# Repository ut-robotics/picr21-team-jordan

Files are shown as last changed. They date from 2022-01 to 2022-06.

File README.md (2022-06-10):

## Project in competitive robotics 2021
</br>

**Credits:**</br>
Programming - **Leonid Tsigrinski**</br>
Mechanics - **Veronika Podliesnova** </br>
Electronics and firmware - **Valentin Resapow** </br>

<details><summary>Photos of Robot and PCB</summary>
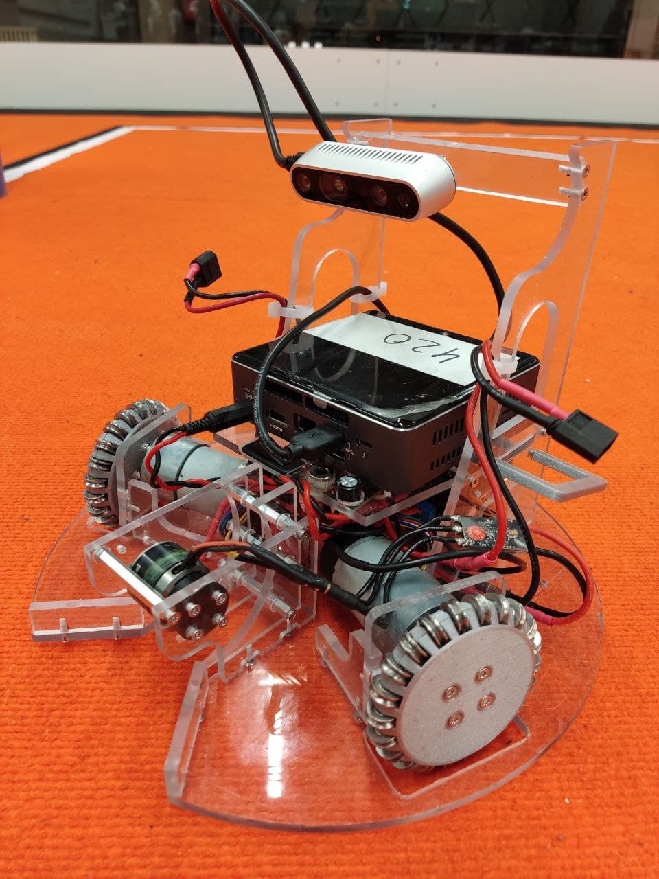
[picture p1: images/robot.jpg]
</br>
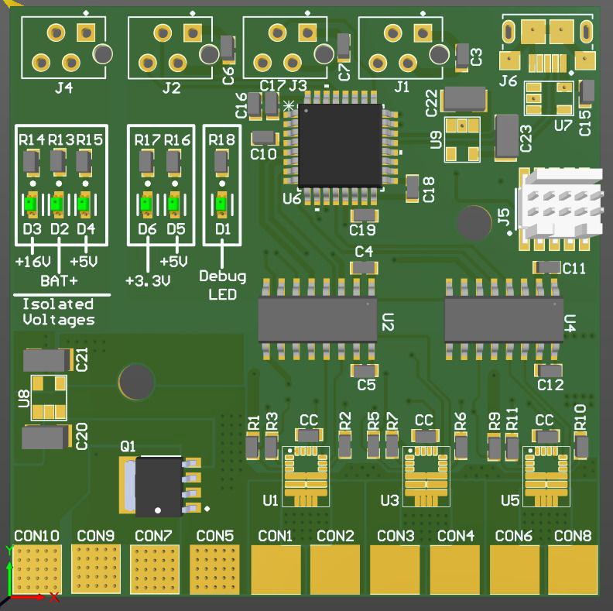
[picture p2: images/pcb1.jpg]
</br>
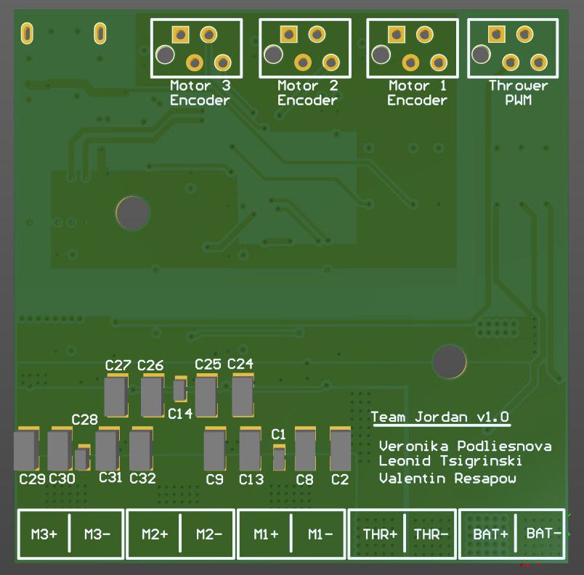
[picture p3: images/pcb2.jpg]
</br>
</details>

**Installation:**</br>
Move to project folder and run `python3.7 -m pip install -r requirements.txt`
Then go to the `.segment_module` folder and run `pip install .` 
Doesen't tested on other python version.</br>

**Used modules/libraries:**</br>
`Numpy` for image processing operations.</br>
`OpenCV` as optional GUI module.</br>
`Pyrealsense2` for realsense camera configuration and working with (especially getting depth).</br>
`Pyserial` for sending motor speed values (HW communication).</br>
`Websockets` for receiveng commands from referee. </br>
`Pynput` for robot manual control. </br>

**How to run the robot?:**</br>
Make sure, that you run first `image_calibration.py` file. Adjust all colors to be detected. Edit ip and port of the referee in `main.py` file, then run it. It you don't have any referees with their servers near by, run `_referee_server.py` . In server shell, you can send commands like "blue", "rose", and "stop", that will run the robot. In main shell, you can press the G to take manual control.

**Game logic:**  
Basically, there are two threads (asyncio coroutines), socket listener thread listens to to referee JSON data and fills global queue variable with it. Game Logic thread firstly checks if manual control enabled. Then checks if global queue variable were filled with commands. If it's a start command (with target basket), then the robot reads the camera image, gets the depth of the basked as well as coordinates of the basket and the balls. Then the robot selects the closest ball and moves to it, and for one iteration enables state machine algorithm. Every iteration state remains remembered. State machine by itself, it's just few steps:

-   find a ball (basically rotate)
-   get to a ball (calculate distance between ball x, y coords and the center coords. Distance is in linear dependency with axes speed)
-   find a basket (rotate around the ball until basket and the ball isn't centered)
-   throw (calculate throwing speed depends on the distance, linear dependency as well)

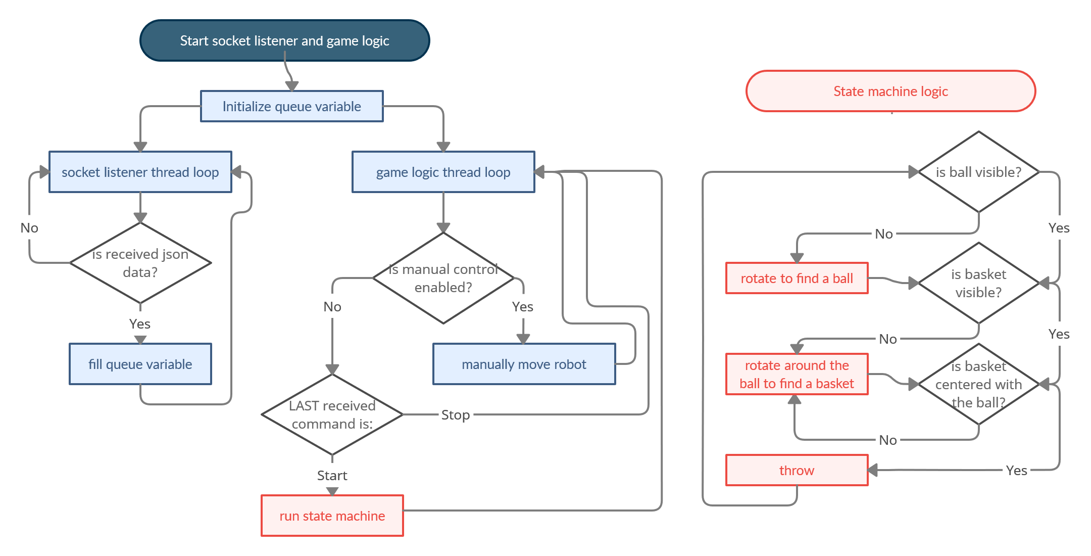
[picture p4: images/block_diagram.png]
</br>

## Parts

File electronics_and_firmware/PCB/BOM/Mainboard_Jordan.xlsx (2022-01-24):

Comment | Description | Designator | Footprint | LibRef | Quantity
Cap Semi | Capacitor (Semiconductor SIM Model) | C1, C3, C4, C5, C6, C7, C10, C11, C12, C14, C15, C16, C17, C18, C19, C28 | 1608[0603] | Cap Semi | 16
Cap Semi | Capacitor (Semiconductor SIM Model) | C2, C8, C9, C13, C20, C21, C22, C23, C24, C25, C26, C27, C29, C30, C31, C32 | C1206 | Cap Semi | 16
Res3 | Resistor | CC, R1, R2, R3, R5, R6, R7, R9, R10, R11, R13, R14, R15, R16, R17, R18 | J1-0603 | Res3 | 18
Moter1 + |  | CON1 | con_soldering | Con_soldering | 1
Motor1 - |  | CON2 | con_soldering | Con_soldering | 1
Motor2 + |  | CON3 | con_soldering | Con_soldering | 1
Motor2 - |  | CON4 | con_soldering | Con_soldering | 1
Thrower + |  | CON5 | con_soldering | Con_soldering | 1
Motor3 + |  | CON6 | con_soldering | Con_soldering | 1
Thrower - |  | CON7 | con_soldering | Con_soldering | 1
Motor3 - |  | CON8 | con_soldering | Con_soldering | 1
BAT+ |  | CON9 | con_soldering | Con_soldering | 1
BAT- |  | CON10 | con_soldering | Con_soldering | 1
LTST-C190GKT | LED GREEN CLEAR CHIP SMD | D1, D2, D3, D4, D5, D6 | FP-LTST-C190GKT-MFG | CMP-22017-000005-2 | 6
Encoder_1 | Micro-MaTch 4 Position 1.27 mm Pitch Vertical Female-on-Board Connector | J1 | TE_7-215079-4 | Con_4_encoder | 1
Encoder_2 | Micro-MaTch 4 Position 1.27 mm Pitch Vertical Female-on-Board Connector | J2 | TE_7-215079-4 | Con_4_encoder | 1
Encoder_3 | Micro-MaTch 4 Position 1.27 mm Pitch Vertical Female-on-Board Connector | J3 | TE_7-215079-4 | Con_4_encoder | 1
PWM_thrower | Micro-MaTch 4 Position 1.27 mm Pitch Vertical Female-on-Board Connector | J4 | TE_7-215079-4 | Con_4_encoder | 1
FTSH-105-XX-X-DV | Connector Header Surface Mount 10 position 0.050" (1.27mm) | J5 | SAMTEC_FTSH-105-XX-X-DV | FTSH-105-XX-X-DV | 1
10118193-0001LF | USB - micro B USB 2.0 Receptacle Connector 5 Position Surface Mount, Right Angle; Through Hole | J6 | FCI_10118193-0001LF | 10118193-0001LF | 1
BUK6Y10-30P |  | Q1 | TRANS_PSMN5R5-60YS,115 | BUK6Y10-30P | 1
PDRV8243HRXYQ1 |  | U1, U3, U5 | DRV8243_motor_driver | PDRV8243HRXYQ1 | 3
MAX14930AASE+ | No Description Available | U2, U4 | 21-0041_S16+1_MXM | MAX14930AASE+ | 2
STM32G441KBT6 | No Description Available | U6 | LQFP-32 | STM32G441KBT6 | 1
CM1223_ESD |  | U7 | CM1223_ESD | CM1223_ESD | 1
NCV8730 |  | U8 | NCP164CSN330T1G_Voltage_regulator | NCV8730 | 1
NCP164 |  | U9 | NCP164CSN330T1G_Voltage_regulator | NCP164 | 1

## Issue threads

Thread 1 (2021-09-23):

[Mechanics] - Thrower missing chassis assembly

Akustav, 2021-09-23:
The thrower should also be attached to the chassis to better judge if it is fitting into the robot.

Akustav, 2021-09-25:
Based on the model I think the thrower motor is a little too low. When pulling the ball it, the robot can be raised up to 9mm. I would lift the motor around 6 mm and extend the C-shaped ramp to bring it closer to the ball that will be pulled into the thrower.

Image illustrates the balls motion:
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

VORPENV, 2021-09-25:
Done

Akustav, 2021-09-27:
Accidentally put a comment on another task but there is an issue with the internal ramp:

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

Maybe the sketch is a little off and takes a bad reference

VORPENV, 2021-09-27:
The sketch is changed

Akustav, 2021-09-28:
Good. I would change one thing and that is to add a chamfer to the front edge. This reduces the chance that something gets impaled while driving around:
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

VORPENV, 2021-09-29:
Done

maidlam, 2021-09-30:
Resolved

Closed 2021-09-30.

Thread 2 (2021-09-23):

[Mechanics] - Ramp spacers to close to ball

Akustav, 2021-09-23:
The ball can hit the spacers holding everything together. This can create issues for the trowing.
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

Akustav, 2021-09-25:
This hole is still too close, I think:
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

VORPENV, 2021-09-27:
Position was changed

Akustav, 2021-09-28:
Hey! The third (top most hole) seems to clip into the ball a little. You can make the distance of every hole equal. This guarantees that all of them stay far enoguh away from the trajectory of the ball.

VORPENV, 2021-09-29:
Done

maidlam, 2021-09-30:
Resolved

Closed 2021-09-30.

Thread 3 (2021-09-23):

[Mechanics] - Weird spacer lengths

Akustav, 2021-09-23:
Spacer sizing for these specific spacers is 11.6mm. They should most likely be 12mm
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

Akustav, 2021-09-25:
Quick question: How will they be fastened to each other? Currently, all spacers are female-female. Will you have a long bolt in there or something else?

VORPENV, 2021-09-25:
The middle spacers will be FF, other - FM. I don't know how exactly show it in the model

Akustav, 2021-09-27:
You can have the spacers modelled out like that, so they are FF or MM. Then it is easy to see what you want to do. If you modify the spacer models on the sides we can close this issue.

Akustav, 2021-09-28:
OK

Closed 2021-09-28.

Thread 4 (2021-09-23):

[Mechanics] - detail thickness wrong

Akustav, 2021-09-23:
This components thickness is 4.5mm. It should be 4.8mm
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

Akustav, 2021-09-25:
Resolved.

Closed 2021-09-25.

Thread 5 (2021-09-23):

[Mechanics] - add rigidity to frame

Akustav, 2021-09-23:
The thrower motor frame could need some rigidity. If you add a spacer somewhere there, it should increase throw consistency
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

Akustav, 2021-09-25:
Resolved.

Closed 2021-09-25.

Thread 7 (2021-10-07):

[Mechanics] - current feedrates  too large

Akustav, 2021-10-07:
I think the current state of the mill does not allow for 1000mm/min feedrates. I would suggest at most 800mm. You can also reduce RPM to around 16000 in this case.

Akustav, 2021-10-09:
Seems fine

Closed 2021-10-09.

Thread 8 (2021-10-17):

Use pyrealsense2

ReikoR, 2021-10-17:
Consider using pyrealsense2 instead of OpenCV VideoCapture. Manually changing exposure time and disabling automatic white balance in code should be easier with pyrealsense2. Automatic exposure and white balance will change camera image colors and cause threshold levels to not work.

ReikoR, 2021-10-31:
pyrealsense2 is being used in addition to OpenCV VideoCapture.

Closed 2021-10-31.

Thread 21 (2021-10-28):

Can't establish Remote Desktop connection.

Leonid-98, 2021-10-28:
I need to mention, that ssh connection (via terminal) works fine, so this asked question is not that critical. </br>
When i install any of the remote desktop solutions (VNC, TeamVeiwer, Ubuntu built-in remote desktop), this works as long, as i have physically connected monitor. When i plug off the cable from the robot PC, image just freezes. I even tried to plug empty HDMI cable, but without the monitor, it doesn't help. Only solution, that i Googled, is was to use physical HDMI Dummy Plug. Is there software solutions as well? Maybe someone else faced this issue before?

Leonid-98, 2021-11-09:
`sudo apt-get install xserver-xorg-video-dummy`
`sudo apt-get install server-xorg-video-dummy-hwe-18.04`
`cd /usr/share/X11/xorg.conf.d/`
`nano xorg.conf`:
<br>
```
Section "Device"
    Identifier  "Configured Video Device"
    Driver      "dummy"
EndSection

Section "Monitor"
    Identifier  "Configured Monitor"
    HorizSync 31.5-48.5
    VertRefresh 50-70
EndSection

Section "Screen"
    Identifier  "Default Screen"
    Monitor     "Configured Monitor"
    Device      "Configured Video Device"
    DefaultDepth 24
    SubSection "Display"
    Depth 24
    Modes "1024x800"
    EndSubSection
EndSection
```

Leonid-98, 2021-11-09:
because ssh is enabled on boot, i can turn this off just by hiding config file

Closed 2021-11-09.

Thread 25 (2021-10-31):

Use serial.tools.list_ports

ReikoR, 2021-10-31:
https://github.com/ut-robotics/picr21-team-jordan/blob/b0aeef8138876d4ae275fab5b78f5c8cd555717f/main_folder/move_function.py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

Use [serial.tools.list_ports](https://pyserial.readthedocs.io/en/latest/tools.html) and port info to find the correct serial port.

Serial port number can change and it's more reliable to find the correct port name than to hardcode it.

Leonid-98, 2021-11-01:
**fixed**<br>
https://github.com/ut-robotics/picr21-team-jordan/blob/5ba7878f3f30b542db5018d997705efe433d6058/main_folder/robot_movement.py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

ReikoR, 2021-11-02:
It would be better if you don't use the entire `hwid` string to find the correct port. `VID:PID=0483:5740` should be what you need, because it doesn't change with different STM32 microcontrollers. `SER` should be unique to the microcontroller and will be different when you have a new or different mainboard. `LOCATION` should be the physical USB port location and will change if the mainboard is connected to different USB port.

Leonid-98, 2021-11-02:
@ReikoR
https://github.com/ut-robotics/picr21-team-jordan/blob/9c5d97e00fe527b5110b865500421555665f3b46/main_folder/robot_movement.py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

ReikoR, 2021-11-02:
It would be better if you declare the `serial_port` variable outside the for loop and raise an exception when serial port was not found.

For example something like this:
```python
from typing import Optional

class SerialPortNotFound(Exception):
    pass

STM_32_HWID = "USB VID:PID=0483:5740"
WHEEL_ANGLES = [120, 0, -120]

class RobotMovement:
    def __init__(self):
        serial_port: Optional[str] = None
        ports = serial.tools.list_ports.comports()
        devices = {}

        for port, _, hwid in sorted(ports):
            devices[hwid] = port

        for hwid in devices.keys():
            if STM_32_HWID in hwid:
                serial_port = devices[hwid]
                break

        if serial_port is None:
            raise SerialPortNotFound("Serial port not found")

        self.ser = serial.Serial(serial_port, 115200)
```

Leonid-98, 2021-11-03:
@ReikoR <br>
**fixed**
https://github.com/ut-robotics/picr21-team-jordan/blob/d943730a70d844ba020a2a85a0d25d82a156d238/main_folder/robot_movement.py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

Closed 2021-11-03.

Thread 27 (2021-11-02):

[Mechanics] - how thick the front covers have to be

Akustav, 2021-11-02:
Was wondering how thick this area should be:

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

If it is structurally unimportant it could be made thinner to quicken up the printing of the wheel. Also the thickness should be a divisible of 0.3 or the layer height of the printer.

VORPENV, 2021-11-04:
I've divided the thickness by approximate 1 mm from both sides

Akustav, 2021-11-07:
OK

Closed 2021-11-07.

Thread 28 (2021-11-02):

[Mechanics] - change way roller shafts are retained

Akustav, 2021-11-02:
I would suggest changing the way how rollers sit inside the wheel housing. Currently you have 2 semicircles that enclose the shaft but you can encounter alignment issues due to the more complex matching between 2 moving semi-circles.

I would suggest a slot that is as deep as the shafts diameter and a flat surface retains this shaft in the housing.

A picture to illustrate:
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

VORPENV, 2021-11-04:
Do you mean that is it better to create the slot for the roller's shaft in one "semi-wheel" ? And the second "semi-wheel" will have this flat surface?

Akustav, 2021-11-07:
A deep slot for the shaft is better than 2 half-circles retaining it. I would change the design to have a deep groove for the shaft and a flat surface that holds the roller in.

Akustav, 2021-11-11:
Seems good

Closed 2021-11-11.

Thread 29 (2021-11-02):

[Mechanics] - screw space

Akustav, 2021-11-02:
This is more of a question and less of an issue but you need exact length socket set screws here. I hope you accounted for it.

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

VORPENV, 2021-11-04:
Now I created small holes for screws

VORPENV, 2021-11-11:
I plan to use set screw, so I don't need such screw spaces

Closed 2021-11-11.

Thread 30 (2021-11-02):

[Mechanics] - drill through fastener if possible to simplify threading

Akustav, 2021-11-02:
I suggest threading through the wheel shaft mount to simplify threading:

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

Seems like one hole is harder to do since it collides with the crossing hole. Does it need a full-length hole?

Closed 2021-11-02.

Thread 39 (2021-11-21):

Improve code structure

ReikoR, 2021-11-21:
Some suggestions:

1. Create separate file/class for camera.  Camera can return RGB and optionally depth frames.
2. Create separate file/class for image processing. Image processing functions from `ImageGetter` and `ImageCalibraion` should be moved into this class. Frame from camera can be given as an argument to image processor's processing method.
3. Object (balls, baskets) locations from image processing can be given to the state machine.
4. Image calibration can use camera and image processing classes.
5. `ImageGetter` class should have different name as it's the main class and probably should not inherit from `ImageCalibraion` class.

Leonid-98, 2021-11-21:
@ReikoR
I did as you said:
main class gets image (from `Camera` class), gets coordinates of the objects (using `ImageProcessing` class) and sends coordinates to the `StateMachine` class. Also, all game info is sent into `Gui `class. In main class i have also `SocketListener` as parallel to main thread. It sends all socket data to the list, and main class checks that list every iteration.

Pushed changes into `not_tested` branch

Closed 2021-11-21.

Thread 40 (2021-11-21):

Too many typos

ReikoR, 2021-11-21:
Some examples:

https://github.com/ut-robotics/picr21-team-jordan/blob/9e5311730d60695c8be9be84ec046d4377a3e32b/main_folder/image_getter.py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

ImageCalibraion -> ImageCalibration
apllyes -> applies
StateMahchine -> StateMachine

https://github.com/ut-robotics/picr21-team-jordan/blob/9e5311730d60695c8be9be84ec046d4377a3e32b/main_folder/image_getter.py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

interrurpt -> interrupt
curent -> current

Leonid-98, 2021-11-21:
@ReikoR fixed all typos with `code spell checker` extension

ReikoR, 2021-11-21:
`class ImageCalibraion` should also be fixed.

Leonid-98, 2021-11-22:
@ReikoR
Fixed that exact typo, everything looks ok, and extension doesen't see any typos as well

Closed 2021-11-23.

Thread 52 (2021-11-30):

Camera resource is opened but never closed

Akustav, 2021-11-30:
https://github.com/ut-robotics/picr21-team-jordan/blob/2ab4613d39a6d57e361e7e64e6009ab22df023fe/main_folder/main.py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

You should close the camera even after an exception or similar is thrown. Currently it is closed after the while loop ends.

Leonid-98, 2021-12-01:
@Akustav
https://github.com/ut-robotics/picr21-team-jordan/blob/c8c0c9cda4c80c28e4c8290ae943c9211dc9dea1/main_folder/main.py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

Closed 2021-12-01.

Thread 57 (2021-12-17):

[Mechanics] - wheel body needs hole so it can be assesmbled

Akustav, 2021-12-17:
Currently the motor shaft interferes with the wheel body:

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

VORPENV, 2021-12-17:
Done

Closed 2021-12-18.

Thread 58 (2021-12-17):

[Mechanics] - hole size wrong on motor mounts

Akustav, 2021-12-17:
These holes in the motor points should be 2.5 mm since they will have threads.

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

VORPENV, 2021-12-17:
Done

Akustav, 2021-12-18:
I actually meant the other way around. Holes on this need to be 2.5mm
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

VORPENV, 2021-12-18:
Done

Closed 2021-12-18.

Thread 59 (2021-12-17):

[Mechanics] - dogbones missing at switch

Akustav, 2021-12-17:
Missing cuts here:
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

VORPENV, 2021-12-17:
Done

Closed 2021-12-18.

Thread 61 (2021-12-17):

[Mechanics] - missing mounting holes for PC

Akustav, 2021-12-17:
No mounting holes on the top plate:

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

VORPENV, 2021-12-18:
Done

Closed 2021-12-18.

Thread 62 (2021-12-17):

[Mechanics] - missing dogbones on top plate mount area

Akustav, 2021-12-17:
Dogbones should also be here:

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

VORPENV, 2021-12-17:
Done

Closed 2021-12-18.

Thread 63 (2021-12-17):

[Mechanics] - way to remove battery may be problematic

Akustav, 2021-12-17:
I am not sure but it can be that the camera might interfer with battery swapping here. Not sure of a good way to visualize it. Maybe you can slip it inside but not 100% sire.

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

VORPENV, 2021-12-17:
Will it change the angle position of the camera?

Akustav, 2021-12-18:
This might not be an issue, I think the battery can be slipped inside. Just pointing it out since I am not 100% sure

VORPENV, 2022-01-24:
Now everything is okay

Closed 2022-01-26.

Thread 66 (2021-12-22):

SocketDataGetter instance is named camera_image

ReikoR, 2021-12-22:
https://github.com/ut-robotics/picr21-team-jordan/blob/fc84323724f5fff3af8c989fcdce25333d1a9085/main_folder/main.py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

Better name should be used.

And `pass` is not needed/should not be used at the end of a function.

Leonid-98, 2021-12-24:
https://github.com/ut-robotics/picr21-team-jordan/blob/79880c195dfcbbf2ae8e234e2cfa73f5677db614/main_folder/main.py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

Closed 2021-12-26.

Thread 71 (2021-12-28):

Programmer connector grounds connected incorrectly

ReikoR, 2021-12-28:
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

GND should be connected to pins 3, 5 and 9.

More information here:
https://reikor.github.io/picr21-basketball-robot-guide/electronics/schematic.html

ReikoR, 2021-12-29:
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

Pin 7 should not be connected to GND.

From programmer's [user manual](https://www.st.com/resource/en/user_manual/dm00555046-stlinkv3mods-and-stlinkv3mini-mini-debuggersprogrammers-for-stm32-stmicroelectronics.pdf):

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

ReikoR, 2021-12-31:
Still incorrect on the PCB:

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

Closed 2021-12-31.

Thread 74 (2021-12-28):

Add decoupling capacitor to MCU NRST pin

ReikoR, 2021-12-28:
Recommendation from [datasheet](https://www.st.com/resource/en/datasheet/stm32g441kb.pdf) under _Figure 27. Recommended NRST pin protection_:
> 1\. The reset network protects the device against parasitic resets.
> 3\. The external capacitor on NRST must be placed as close as possible to the device.

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

Closed 2021-12-29.

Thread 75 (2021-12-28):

Thrower connector does not need 5V

ReikoR, 2021-12-28:
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

Thrower motor controllers have two wires for signal: GND and PWM.

Current controllers have following pinout:
1 - GND
2 - PWM
3 - NC (not connected)
4 - NC

Closed 2021-12-29.

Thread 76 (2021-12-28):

Avoid overlapping schematics objects

ReikoR, 2021-12-28:
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

Closed 2021-12-29.

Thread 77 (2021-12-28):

Use wider gap between isolated sides

ReikoR, 2021-12-28:
There should be physical gap between isolated sides. Avoid overlapping copper on different sides.

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

ReikoR, 2021-12-29:
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

Thrower connector and LEDs need to be moved to the other side. It would also be better if tracks were kept over the inner GND polygons.

Closed 2021-12-31.

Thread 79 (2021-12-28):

Create Board Outline Clearance rule

ReikoR, 2021-12-28:
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

Closed 2021-12-29.

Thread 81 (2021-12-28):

USB connector needs to be closer to board edge

ReikoR, 2021-12-28:
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

USB connector has downwards edge, that will interfere with the PCB.

Picture from another board:

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

valli96, 2021-12-29:
I hope this is the correct distance from the edge

ReikoR, 2021-12-29:
3D model on the footprint would help with that.

From another board it seems that around 1.6 mm from the slot hole to board edge might be the max:

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

You have right now 1.85mm, which is too much:

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

The lines on Mechanical 13 layer are also useful:

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

valli96, 2021-12-31:
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

I hope this will be fine

Closed 2021-12-31.

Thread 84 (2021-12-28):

Move decoupling capacitors closer to components

ReikoR, 2021-12-28:
Shorter tracks have lower inductance.

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

valli96, 2021-12-29:
I have brought all the capacitors as close as components now.
The footprints prohibit bringing them even closer

Closed 2021-12-29.

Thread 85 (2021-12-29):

All capacitor values are 100pF

ReikoR, 2021-12-29:
Example:
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

Most of them should be 100nF or 10uF.

ReikoR, 2021-12-31:
All other capacitors are still 100pF.

One example:

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

ReikoR, 2021-12-31:
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

1 uF should probably be 10 uF on VM pin.

Also all resistors are 1K:

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

Closed 2022-01-01.

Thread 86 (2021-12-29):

Fix DRC errors

ReikoR, 2021-12-29:
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

ReikoR, 2021-12-31:
Try to fix USB footprint. For some reason there is hole inside the slot in original footprint. The hole can be deleted.

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

valli96, 2021-12-31:
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
If I move the USB too far to the edge, I get some DRC error

ReikoR, 2021-12-31:
This line can be aligned with board edge:

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

To fix Hole Size Constraint Violations, increase Maximum value in HoleSize rule:

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

[JLCPCB Capabilities](https://jlcpcb.com/capabilities/Capabilities):
Drill Hole Size: 0.20mm- 6.30mm

valli96, 2022-01-01:
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
If I aligned  the connector with the board edge, I have a distance of 2.1mm

ReikoR, 2022-01-01:
For issue #81, I measured distance from the edge of the slot, not from the center.

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

Closed 2022-01-01.

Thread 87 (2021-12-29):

Improve silkscreen on PCB

ReikoR, 2021-12-29:
**1. Adjust line width.**

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

JLCPCB recommendations:
Minimum Line Width: 6 mil (0.153mm)
Minimum text height: 40 mil (1.0mm)

https://jlcpcb.com/capabilities/Capabilities

You have:
Text Height: 0.8 mm
Stroke Width: 0.254 mm

Height of 0.8 mm probably works, but it would be better to use line width of 0.15 mm, so that text would turn out readable.

**2. Avoid placing designators on pads and under components.**

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

**3. Use tented vias.**

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

Probably the easiest option to use tented vias, is to create new Solder Mask Expansion rule for vias:

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

**4. Add additional descriptive text**

Instead of designators you might want to mark which pad is battery plus and battery minus and which output is which.

ReikoR, 2021-12-31:
J1 is on pads.

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

Closed 2021-12-31.

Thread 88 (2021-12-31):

Move ESD protection closer to USB connector

ReikoR, 2021-12-31:
Having ESD protection closer helps to avoid ESD spikes from propagating to other components.

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

ReikoR, 2021-12-31:
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

Rotating the ESD protection component would help to improve the USB signal routing:

Something like this:

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

valli96, 2022-01-01:
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

Closed 2022-01-01.

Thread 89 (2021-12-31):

Avoid routing signals on GND layers

ReikoR, 2021-12-31:
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

Splits in ground might cause electric fields to spread out, which might cause crosstalk on other signals.

Something like this would be better:

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

valli96, 2021-12-31:
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
Now it is routed through over the bottom layer

ReikoR, 2021-12-31:
Now you are splitting up +16V and leaving narrow copper for high currents.

It's better to route nSLEEP near PGND polygon:

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

valli96, 2022-01-01:
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

Closed 2022-01-01.

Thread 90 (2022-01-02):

Gerber files and Drill files export

valli96, 2022-01-02:
Altium has the function to export both Gerber files and drill files as one file. This should also be ok for JLC PCB.

Are the settings right?
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

ReikoR, 2022-01-02:
X2 should probably work. I have used regular gerber (RS-274X).

From this [KiCad forum topic](https://forum.kicad.info/t/apologies-from-atommann-an-engineer-from-jlcpcb-about-gerber-x2-files-at-jlcpcb/26847/59), it seems JLCPCB is converting X2 format to RS-274X format for the software they are using.

For layers to plot you also need Mechanical 1 for board outline. You should not need keep-out and pad master layers.

valli96, 2022-01-02:
I updated the zip file and added the Mechanical 1 layer

Closed 2022-01-09.

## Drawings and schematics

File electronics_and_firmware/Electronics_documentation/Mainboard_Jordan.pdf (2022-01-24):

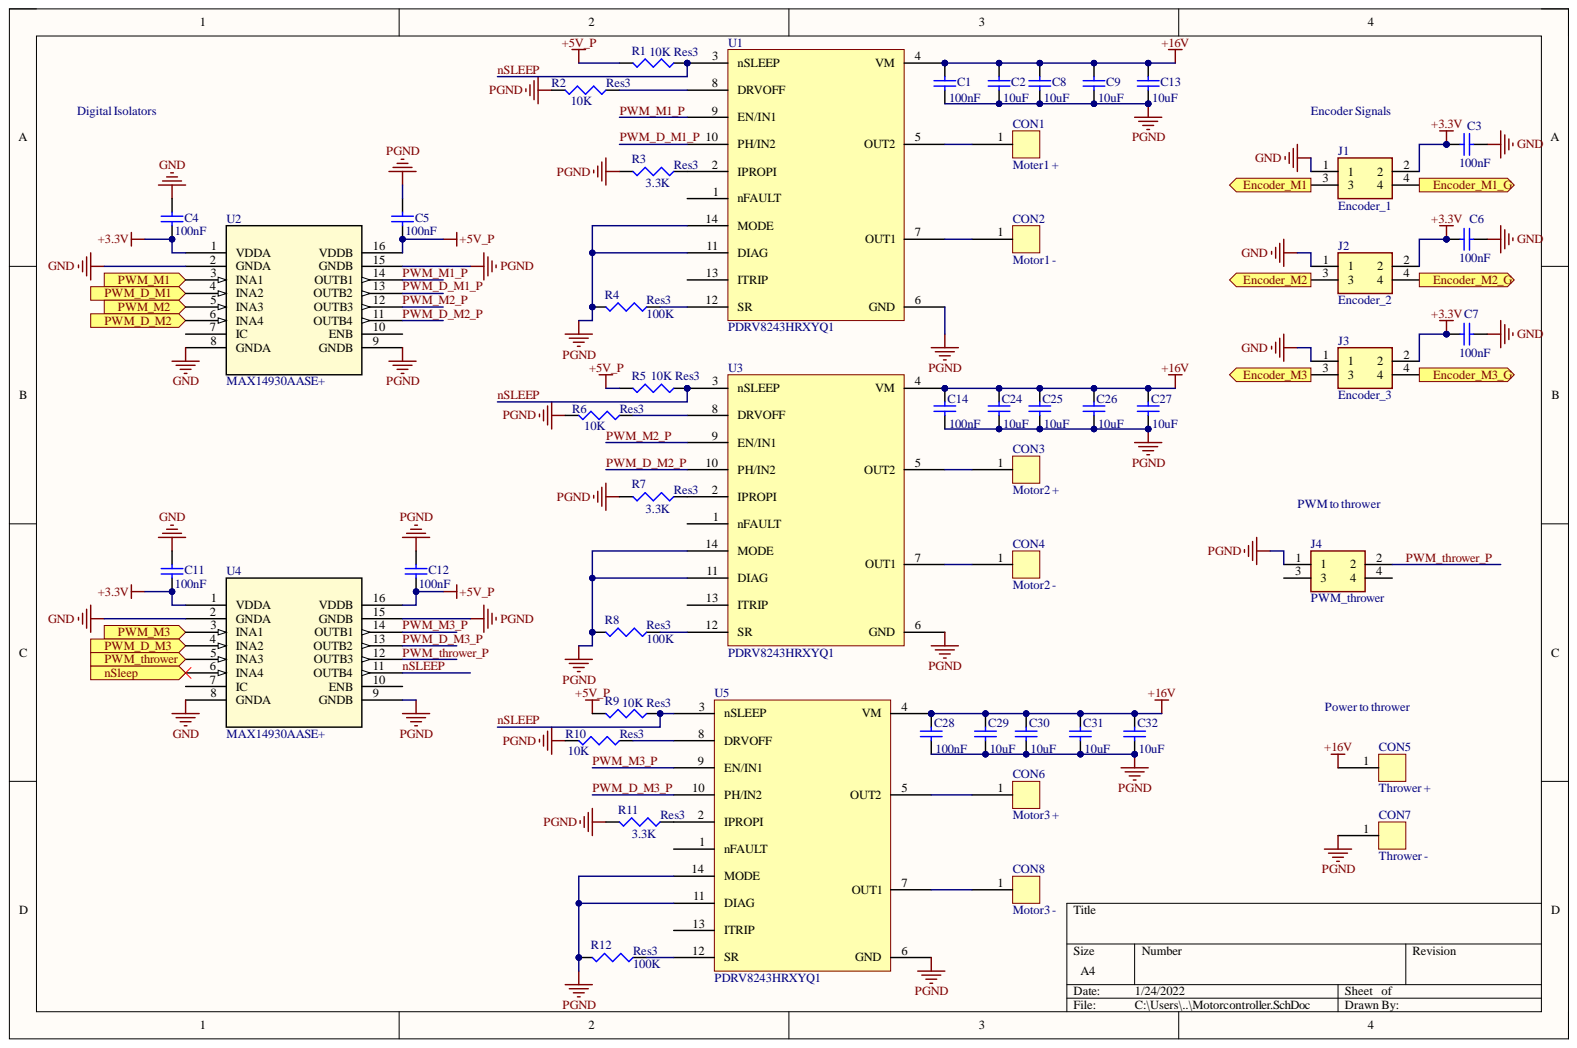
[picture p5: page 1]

Size A4 | Number | Revision

Date: 1/24/2022 | Sheet of
File: C:\Users\..\Motorcontroller.SchDoc | Drawn By:

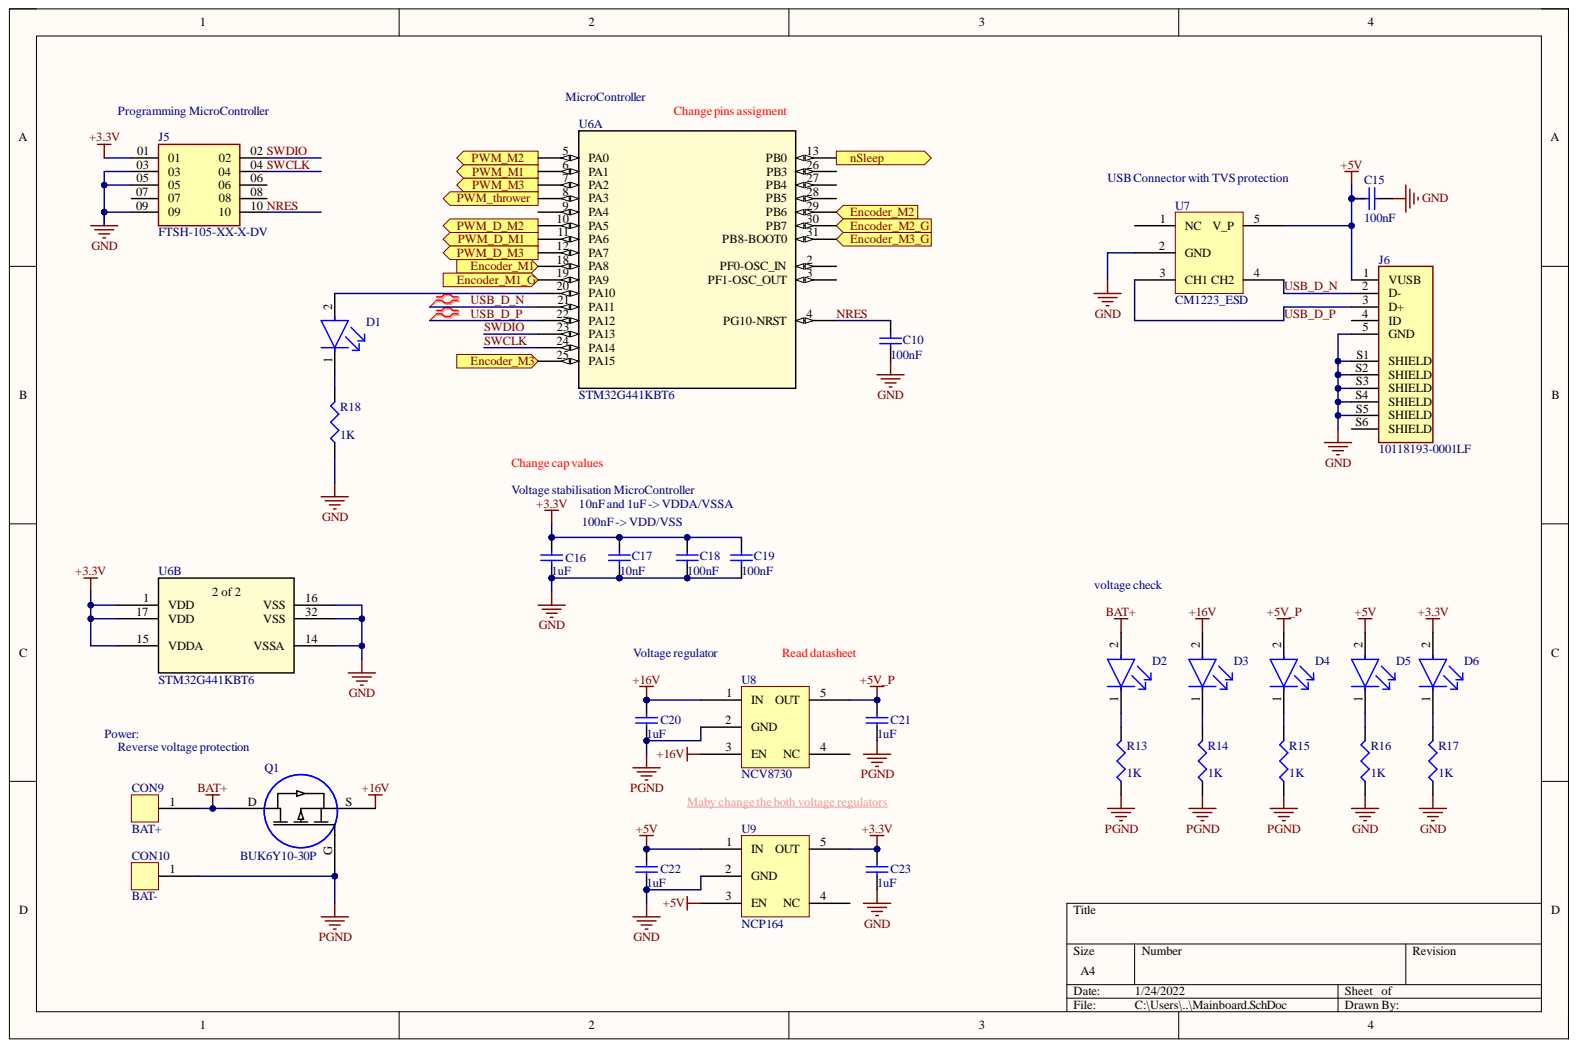
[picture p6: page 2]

USBConnector with TVS protection

USB_D_N | D- 2

Maby change the both voltage regulators

Size A4 | Number | Revision

Date: 1/24/2022 | Sheet of
File: C:\Users\..\Mainboard.SchDoc | Drawn By:

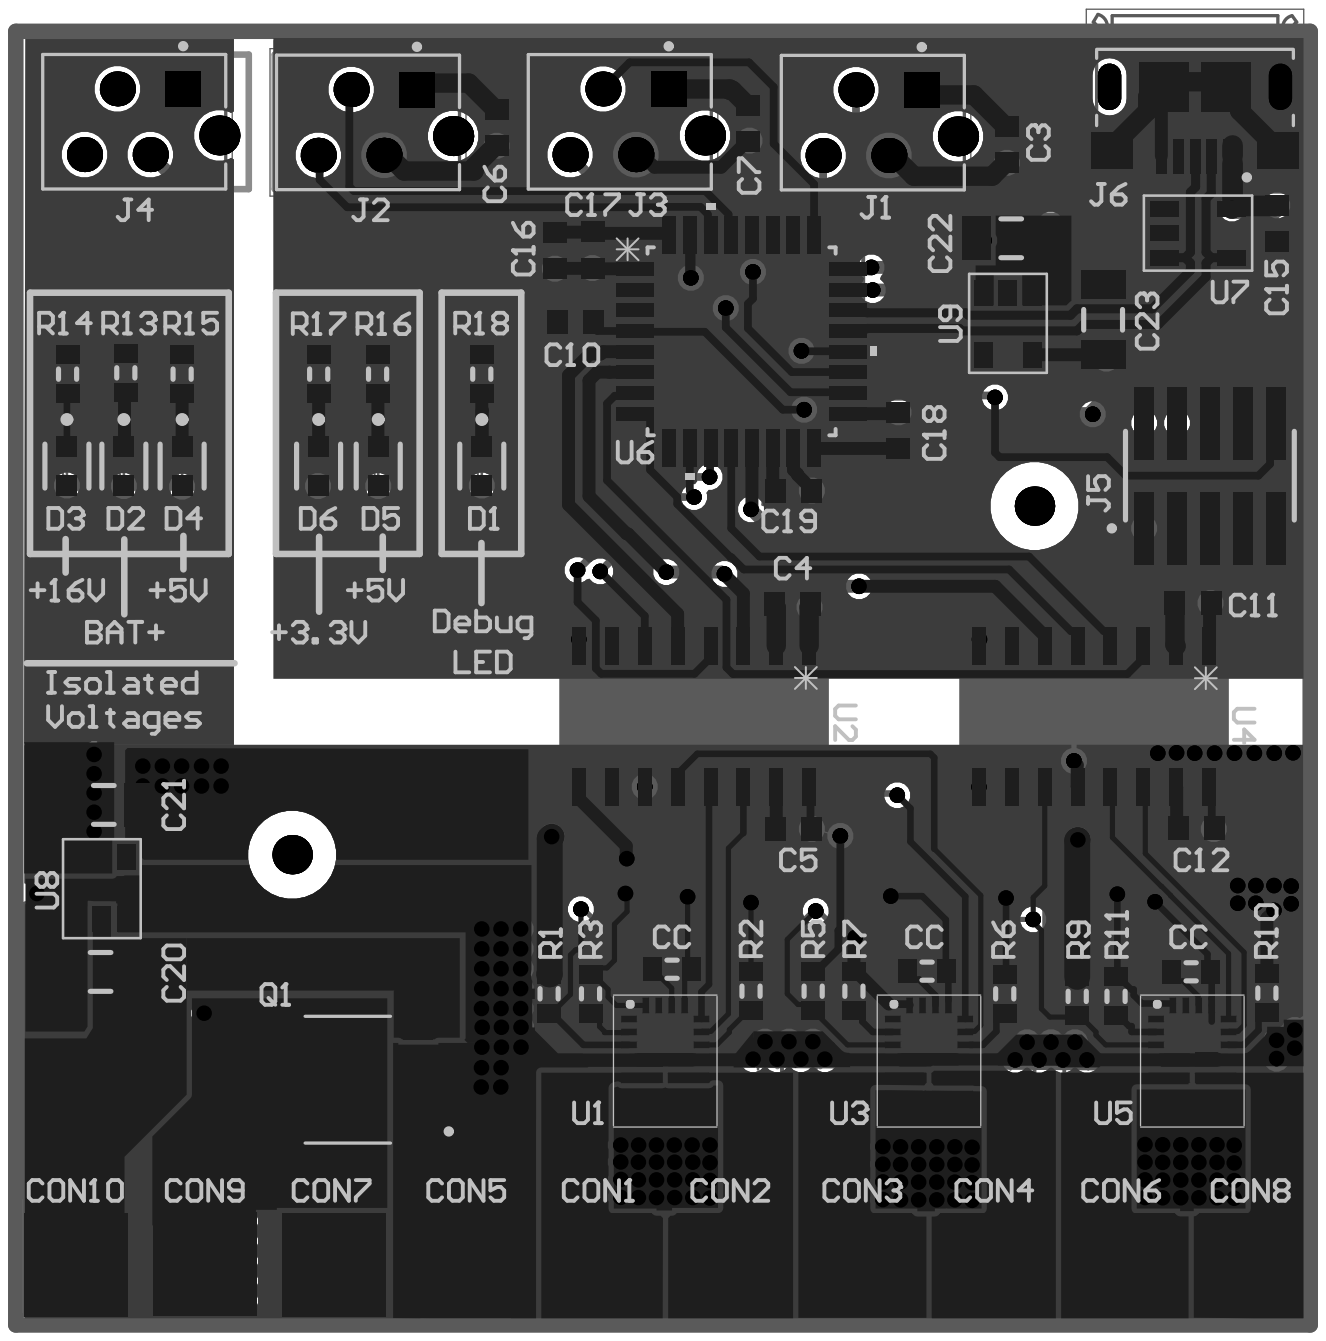
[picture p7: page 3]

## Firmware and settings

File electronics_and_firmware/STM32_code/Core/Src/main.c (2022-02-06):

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
/* Includes ------------------------------------------------------------------*/
#include "main.h"
#include "usb_device.h"

/* USER CODE BEGIN Includes */
#include "usbd_cdc_if.h"
/* USER CODE END Includes */

TIM_HandleTypeDef htim1;
TIM_HandleTypeDef htim2;
TIM_HandleTypeDef htim4;
TIM_HandleTypeDef htim6;
TIM_HandleTypeDef htim8;
TIM_HandleTypeDef htim15;

void SystemClock_Config(void);
static void MX_GPIO_Init(void);
static void MX_TIM2_Init(void);
static void MX_TIM1_Init(void);
static void MX_TIM4_Init(void);
static void MX_TIM8_Init(void);
static void MX_TIM15_Init(void);
static void MX_TIM6_Init(void);
/* USER CODE BEGIN 0 */

 //Frequency Register f_main = 160MHz  ARR = 65535  -> f_main/ARR ~2444
int16_t P_factor = 2500;
int16_t D_factor = 10;
int16_t I_factor = 2;

int32_t cumulativeError_M1 = 0;
int32_t cumulativeError_M2 = 0;
int32_t cumulativeError_M3 = 0;



typedef struct Command { //
  int16_t speed1;
  int16_t speed2;
  int16_t speed3;
  uint16_t throwerSpeed;
  uint16_t delimiter; //
} Command;
Command command = {.speed1 = 0, .speed2 = 0, .speed3 = 0, .throwerSpeed = 0, .delimiter = 0}; // (4)

typedef struct Feedback { //
  int16_t speed1;
  int16_t speed2;
  int16_t speed3;
  uint16_t delimiter;
} Feedback;

typedef struct Setpoints { //
  int16_t speed1;
  int16_t speed2;
  int16_t speed3;
} Setpoints;
Setpoints setpoints = {.speed1 = 0, .speed2 = 0, .speed3 = 0};

typedef struct Motor_pose { //
  int16_t pose_M1;
  int16_t pose_M2;
  int16_t pose_M3;
} Motor_pose;
Motor_pose motor_pose = {.pose_M1 = 0, .pose_M2 = 0, .pose_M3 = 0};

typedef struct Motor_pose_prev { //
  int16_t pose_prev_M1;
  int16_t pose_prev_M2;
  int16_t pose_prev_M3;
} Motor_pose_prev;
Motor_pose_prev motor_pose_prev = {.pose_prev_M1 = 0, .pose_prev_M2 = 0, .pose_prev_M3 = 0};

typedef struct Motor_pose_change { //
  int16_t pose_change_M1;
  int16_t pose_change_M2;
  int16_t pose_change_M3;
} Motor_pose_change;
Motor_pose_change motor_pose_change = {.pose_change_M1 = 0, .pose_change_M2 = 0, .pose_change_M3 = 0};

typedef struct Motor_speed_send { //
	int32_t speed_send_M1;
	int32_t speed_send_M2;
	int32_t speed_send_M3;
} Motor_speed_send;
Motor_speed_send motor_speed_send = {.speed_send_M1 = 0, .speed_send_M2 = 0, .speed_send_M3 = 0};

int32_t currentError_M1  = 0;
int32_t currentError_M2 = 0;
int32_t currentError_M3 = 0;
void PID_Controller(){

	float time_call = 1/100; // this is the time between function calls

	motor_pose_change.pose_change_M1 = motor_pose.pose_M1 - motor_pose_prev.pose_prev_M1;
	motor_pose_change.pose_change_M2 = motor_pose.pose_M2 - motor_pose_prev.pose_prev_M2;
	motor_pose_change.pose_change_M3 = motor_pose.pose_M3 - motor_pose_prev.pose_prev_M3;

	currentError_M1 = setpoints.speed1 - motor_pose_change.pose_change_M1;
	currentError_M2 = setpoints.speed2 - motor_pose_change.pose_change_M2;
	currentError_M3 = setpoints.speed3 - motor_pose_change.pose_change_M3;

	cumulativeError_M1 += currentError_M1;
	cumulativeError_M2 += currentError_M2;
	cumulativeError_M3 += currentError_M3;

	motor_speed_send.speed_send_M1 = currentError_M1 * P_factor - \
			        D_factor * motor_pose_change.pose_change_M1 + \
					I_factor * cumulativeError_M1;

	motor_speed_send.speed_send_M2 = currentError_M2 * P_factor - \
			        D_factor * motor_pose_change.pose_change_M2 + \
					I_factor * cumulativeError_M2;

	motor_speed_send.speed_send_M3 = currentError_M3 * P_factor - \
			        D_factor * motor_pose_change.pose_change_M3 + \
					I_factor * cumulativeError_M3;

	motor_pose_prev.pose_prev_M1 = motor_pose.pose_M1;
	motor_pose_prev.pose_prev_M2 = motor_pose.pose_M2;
	motor_pose_prev.pose_prev_M3 = motor_pose.pose_M3;

}

void processing_values(){

	if (motor_speed_send.speed_send_M1 >= 0){
		HAL_GPIO_WritePin(DIR_M1_GPIO_Port, DIR_M1_Pin, 1);
		if (motor_speed_send.speed_send_M1 > 65535){
			motor_speed_send.speed_send_M1 = 65535;
		}
	}
	else{
		HAL_GPIO_WritePin(DIR_M1_GPIO_Port, DIR_M1_Pin, 0);
		if (motor_speed_send.speed_send_M1 < -65535){
			motor_speed_send.speed_send_M1 = -65535;
		}
		motor_speed_send.speed_send_M1 = -motor_speed_send.speed_send_M1;
	}

	if (motor_speed_send.speed_send_M2 >= 0){
		HAL_GPIO_WritePin(DIR_M2_GPIO_Port, DIR_M2_Pin, 1);
		if (motor_speed_send.speed_send_M2 > 65535){
			motor_speed_send.speed_send_M2 = 65535;
		}
	}
	else{
		HAL_GPIO_WritePin(DIR_M2_GPIO_Port, DIR_M2_Pin, 0);
		if (motor_speed_send.speed_send_M2 < -65535){
			motor_speed_send.speed_send_M2 = -65535;
		}
		motor_speed_send.speed_send_M2 = -motor_speed_send.speed_send_M2;
	}

	if (motor_speed_send.speed_send_M3 >= 0){
		HAL_GPIO_WritePin(DIR_M3_GPIO_Port, DIR_M3_Pin, 1);
		if (motor_speed_send.speed_send_M3 > 65535){
			motor_speed_send.speed_send_M3 = 65535;
		}
	}
	else{
		HAL_GPIO_WritePin(DIR_M3_GPIO_Port, DIR_M3_Pin, 0);
		if (motor_speed_send.speed_send_M3 < -65535){
			motor_speed_send.speed_send_M3 = -65535;
		}
		motor_speed_send.speed_send_M3 = -motor_speed_send.speed_send_M3;
	}

	if (cumulativeError_M1 >= 65535/I_factor) {
		cumulativeError_M1 = 65535/I_factor;
	}
	if (cumulativeError_M2 >= 65535/I_factor) {
		cumulativeError_M2 = 65535/I_factor;
	}
	if (cumulativeError_M3 >= 65535/I_factor) {
		cumulativeError_M3 = 65535/I_factor;
	}

	if (cumulativeError_M1 <= -65535/I_factor) {
		cumulativeError_M1 = -65535/I_factor;
	}
	if (cumulativeError_M2 <= -65535/I_factor) {
		cumulativeError_M2 = -65535/I_factor;
	}
	if (cumulativeError_M3 <= -65535/I_factor) {
		cumulativeError_M3 = -65535/I_factor;
	}


}

void out_put_sleep (){
	  HAL_GPIO_WritePin(GPIOB, GPIO_PIN_0, GPIO_PIN_SET);
	  for (int i = 0; i < 350; i++) {
		  __asm("nop");
	  }
	  HAL_GPIO_WritePin(GPIOB, GPIO_PIN_0, GPIO_PIN_RESET);
	  for (int i = 0; i < 350; i++) {
		  __asm("nop");
	   }
	  HAL_GPIO_WritePin(GPIOB, GPIO_PIN_0, GPIO_PIN_SET);
}


void HAL_TIM_PeriodElapsedCallback(TIM_HandleTypeDef *htim) {

	// ################# read Encoder values ##################
	motor_pose.pose_M1 = (int16_t)TIM4->CNT;
	motor_pose.pose_M2 = (int16_t)TIM8->CNT;
	motor_pose.pose_M3 = (int16_t)TIM1->CNT;

	// scale the value

	PID_Controller();	 // calculate velocities based on a PID controller
	processing_values(); // direction control

	// changes duty cycle of the motors
	TIM2->CCR2 = motor_speed_send.speed_send_M1;
 	TIM2->CCR1 = motor_speed_send.speed_send_M2;
	TIM2->CCR3 = motor_speed_send.speed_send_M3;


}

volatile uint8_t isCommandReceived = 0; // (5)

void CDC_On_Receive(uint8_t* buffer, uint32_t* length) {
	// for testing the serial communication
  if (*length == sizeof(Command)) {
    memcpy(&command, buffer, sizeof(Command));

    if (command.delimiter == 0xAAAA) {
      isCommandReceived = 1;
    }
  }
}
/* USER CODE END 0 */

/**
  * @brief  The application entry point.
  * @retval int
  */
int main(void)
{
  /* MCU Configuration--------------------------------------------------------*/

  /* Reset of all peripherals, Initializes the Flash interface and the Systick. */
  HAL_Init();

  /* Configure the system clock */
  SystemClock_Config();

  /* Initialize all configured peripherals */
  MX_GPIO_Init();
  MX_TIM2_Init();
  MX_TIM1_Init();
  MX_TIM4_Init();
  MX_TIM8_Init();
  MX_TIM15_Init();
  MX_USB_Device_Init();
  MX_TIM6_Init();
  /* USER CODE BEGIN 2 */

  Feedback feedback = { // (1)
      .speed1 = 0,
      .speed2 = 0,
      .speed3 = 0,
      .delimiter = 0xAAAA
  };
  HAL_TIM_Encoder_Start(&htim1, TIM_CHANNEL_1 | TIM_CHANNEL_2); // Encoder 1
  HAL_TIM_Encoder_Start(&htim4, TIM_CHANNEL_1 | TIM_CHANNEL_2); // Encoder 2
  HAL_TIM_Encoder_Start(&htim8, TIM_CHANNEL_1 | TIM_CHANNEL_2);	// Encoder 3
  HAL_TIM_PWM_Start(&htim2, TIM_CHANNEL_1);	// Motor 2
  HAL_TIM_PWM_Start(&htim2, TIM_CHANNEL_2); // Motor 1
  HAL_TIM_PWM_Start(&htim2, TIM_CHANNEL_3); // Motor 3
  HAL_TIM_PWM_Start(&htim15, TIM_CHANNEL_2); // thrower motor
  HAL_TIM_Base_Start_IT(&htim6); // Timer for which indicates when to update the motor speeds



  /* USER CODE END 2 */

  /* Infinite loop */
  /* USER CODE BEGIN WHILE */




HAL_GPIO_TogglePin(Debug_LED_GPIO_Port, Debug_LED_Pin); // (3)
HAL_Delay(200);
HAL_GPIO_TogglePin(Debug_LED_GPIO_Port, Debug_LED_Pin); // (3)
HAL_Delay(200);
HAL_GPIO_TogglePin(Debug_LED_GPIO_Port, Debug_LED_Pin); // (3)


//HAL_GPIO_WritePin(DIR_M1_GPIO_Port, DIR_M1_Pin,1);
//HAL_GPIO_WritePin(DIR_M2_GPIO_Port, DIR_M2_Pin,1);
//HAL_GPIO_WritePin(DIR_M3_GPIO_Port, DIR_M3_Pin,1);

//TIM2->CCR1 = 9000;
//TIM2->CCR2 = 9600;
//TIM2->CCR3 = 9500;


TIM15->CCR2 = 3000; // for initialization of the ESP 3000 -> below 1 ms

  while (1)
  {
    /* USER CODE END WHILE */

    /* USER CODE BEGIN 3 */
	    if (isCommandReceived) {
	      isCommandReceived = 0;
	      TIM15->CCR2 = command.throwerSpeed;

	      HAL_GPIO_TogglePin(Debug_LED_GPIO_Port, Debug_LED_Pin); // (3)
//	      HAL_Delay(3);
//	      HAL_GPIO_TogglePin(Debug_LED_GPIO_Port, Debug_LED_Pin); // (3)

	      out_put_sleep();	 // nSleep control
	      setpoints.speed1 = command.speed1;
	      setpoints.speed2 = command.speed2;
	      setpoints.speed3 = command.speed3;

	      feedback.speed1 = motor_pose_change.pose_change_M3; // -> is motor pose 1
	      feedback.speed2 = currentError_M3; // -> is motor pose 2
	      feedback.speed3 = motor_speed_send.speed_send_M3; // -> is motor pose 3


//		  TIM2->CCR2 = command.speed1;
//		  TIM2->CCR1 = command.speed2;
//		  TIM2->CCR3 = command.speed3;


	      CDC_Transmit_FS(&feedback, sizeof(feedback));
	    }
  	  }
  /* USER CODE END 3 */
}

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


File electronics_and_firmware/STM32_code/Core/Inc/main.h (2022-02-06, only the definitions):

#define PWM_M2_Pin GPIO_PIN_0
#define PWM_M2_GPIO_Port GPIOA
#define PWM_M1_Pin GPIO_PIN_1
#define PWM_M1_GPIO_Port GPIOA
#define PWM_M3_Pin GPIO_PIN_2
#define PWM_M3_GPIO_Port GPIOA
#define PWM_Thrower_Pin GPIO_PIN_3
#define PWM_Thrower_GPIO_Port GPIOA
#define DIR_M2_Pin GPIO_PIN_5
#define DIR_M2_GPIO_Port GPIOA
#define DIR_M1_Pin GPIO_PIN_6
#define DIR_M1_GPIO_Port GPIOA
#define DIR_M3_Pin GPIO_PIN_7
#define DIR_M3_GPIO_Port GPIOA
#define Encoder_3_1_Pin GPIO_PIN_8
#define Encoder_3_1_GPIO_Port GPIOA
#define Encoder_3_0_Pin GPIO_PIN_9
#define Encoder_3_0_GPIO_Port GPIOA
#define Debug_LED_Pin GPIO_PIN_10
#define Debug_LED_GPIO_Port GPIOA
#define Encoder_2_0_Pin GPIO_PIN_15
#define Encoder_2_0_GPIO_Port GPIOA
#define Encoder_1_0_Pin GPIO_PIN_6
#define Encoder_1_0_GPIO_Port GPIOB
#define Encoder_1_1_Pin GPIO_PIN_7
#define Encoder_1_1_GPIO_Port GPIOB
#define Encoder_2_1_Pin GPIO_PIN_8
#define Encoder_2_1_GPIO_Port GPIOB

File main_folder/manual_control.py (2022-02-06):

from pynput import keyboard


class ManualController:
    """
    Class that listens to key input and changes robot speed values.
    """
    def __init__(self):
        self.thrower_max_speed = 3000
        self.max_speed = 40
        self.speed_x = 0
        self.speed_y = 0
        self.speed_rot = 0
        self.speed_throw = 0
        self.enable = False
        self.kill = False

    def main(self):
        listener = keyboard.Listener(on_press=self.on_press, on_release=self.nothing)
        listener.start()

    def on_press(self, key):
        if key.char == "g":
            self.enable = True if self.enable == False else False
            print(f"Running manual control = {self.enable}")

        if self.enable:
            try:
                if key.char == "w":
                    self.speed_y = self.max_speed if self.speed_y == 0 else 0
                elif key.char == "s":
                    self.speed_y = -self.max_speed if self.speed_y == 0 else 0
                elif key.char == "d":
                    self.speed_x = self.max_speed if self.speed_x == 0 else 0
                elif key.char == "a":
                    self.speed_x = -self.max_speed if self.speed_x == 0 else 0
                elif key.char == "e":
                    self.speed_rot = int(-self.max_speed / 3) if self.speed_rot == 0 else 0
                elif key.char == "q":
                    self.speed_rot = int(self.max_speed / 3) if self.speed_rot == 0 else 0
                elif key.char == "t":
                    self.speed_rot = 0
                    self.speed_x = 0
                    self.speed_y = 0
                elif key.char == "m":
                    self.speed_throw += 10 if self.speed_throw != self.thrower_max_speed else self.thrower_max_speed
                    print(self.speed_throw)
                elif key.char == "n":
                    self.speed_throw -= 10 if self.speed_throw != 0 else 0
                    print(self.speed_throw)
            # special key pressed
            except AttributeError:
                pass

    def nothing(self, key):
        pass

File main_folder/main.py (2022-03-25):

import asyncio
import time
import json

import cv2
from websockets import connect

from camera import RealsenseCamera
from enums import GameObject, State
from image_processor import ImageProcessor
from manual_control import ManualController
from robot_gui import RobotGui
from robot_movement import RobotMovement
from state_machine import StateMachine

IP = "172.17.89.147"
PORT = 8888
ROBOT_ID = "001TRT"


class GameLogic:
    """
    Main class. Gets frames, applyes image processing to get:
    Ball coord, ball size, basket coord, basket size. Sends values to the StateMachine class
    """

    def __init__(self, enable_gui):
        self.cam = RealsenseCamera()
        self.cam.open()
        self.gui = RobotGui() if enable_gui else None
        self.robot_movement = RobotMovement()
        self.manual_controller = ManualController()
        self.manual_controller.main()
        self.state_machine = StateMachine(self.robot_movement)
        self.image_processor = ImageProcessor(self.cam)

        self.target_basket = GameObject.BASKET_BLUE
        self.robot_id = ROBOT_ID
        self.current_state = State.INITIAL
        self.run = True  # TODO FALSE

        self.enable_gui = enable_gui
        self.fps = 0

    def main(self, socket_data):
        start_time = time.time()

        # check if manual control is enabled
        if self.manual_controller.enable:
            self.robot_movement.move_robot_XY(self.manual_controller.speed_x, self.manual_controller.speed_y, self.manual_controller.speed_rot, self.manual_controller.speed_throw)
        # enable game logic
        else:
            # check for referee commands
            if socket_data:
                command = socket_data.pop(0)
                try:
                    if command["signal"] == "start":
                        index = command["targets"].index(self.robot_id)
                        target_basket = command["baskets"][index]
                        self.target_basket = GameObject.BASKET_BLUE if target_basket == "blue" else GameObject.BASKET_ROSE
                        self.run = True

                    elif command["signal"] == "stop":
                        index = command["targets"].index(self.robot_id)
                        self.run = False
                except ValueError:
                    # target isn't our robot id
                    pass

            # detect all objects
            aligned_depth = True if self.current_state == State.THROW else False
            results = self.image_processor.process_frame(aligned_depth=aligned_depth)
            ball_x, ball_y, ball_radius = -1, -1, -1
            basket_x, basket_y, basket_radius = -1, -1, -1
            basket_dist = -1

            if results.balls:
                ball = results.balls[0]
                ball_x = ball.x
                ball_y = ball.y
                ball_radius = int(ball.width / 2)

            basket = results.basket_b if self.target_basket == GameObject.BASKET_BLUE else results.basket_m
            if basket.exists:
                basket_x = basket.x
                basket_y = basket.y
                basket_radius = int(basket.width / 2)
                basket_dist = int(round(basket.distance * 100))
                    
            # run robot
            if self.run:
                self.current_state = self.state_machine.run_current_state(ball_x, ball_y, basket_x, basket_dist)
            else:
                self.robot_movement.move_robot_XY(0, 0, 0, 0)

            # show gui
            if self.enable_gui:
                ball_info = [ball_x, ball_y, ball_radius, (ball_x, ball_y)]
                basket_info = [basket_x, basket_y, basket_radius, (basket_x, basket_y)]

                self.gui.update_image(results.color_frame)
                self.gui.update_info(self.fps, self.current_state, ball_info, basket_info)
                self.gui.show_gui()
        self.fps = round(1.0 / (time.time() - start_time), 2)


async def run_listener(out_q):
    server = f"ws://{IP}:{PORT}"
    async with connect(server) as websocket:
        while True:
            server_data = await websocket.recv()
            command = json.loads(server_data)
            out_q.append(command)


async def run_game_logic(in_q):
    game_logic = GameLogic(enable_gui=True)

    while True:
        game_logic.main(in_q)
        await asyncio.sleep(0.0001)
        if cv2.waitKey(1) & 0xFF == ord("x"):
            game_logic.robot_movement.move_robot_XY(0, 0, 0, 0)
            break
    game_logic.cam.close()
    if game_logic.enable_gui:
        game_logic.gui.kill_gui()


if __name__ == "__main__":
    loop = asyncio.get_event_loop()
    q = []
    loop.create_task(run_game_logic(q))
    loop.create_task(run_listener(q))
    loop.run_forever()

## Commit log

2021-09-06 Create camera_processing.py
    added example of image processing from prev. course
2021-09-15 socket client-server added
2021-09-23 !big refactor! -- also possibly broke point
    [image_calibration.py, main.py, state_machine.py]
2021-09-24 added Threading, created single-thread and multi-thread main file
2021-10-04 test communication with STM32
2021-10-14 socket input simulation
2021-10-18 tried to fix opened issues
    [image_calibration.py, main.py]
2021-10-18 created emthod draw_info to avoid code spaghetti
    [image_calibration.py, main.py]
2021-10-19 added two examples of image calibration: using cap.read() and pyreralsense
2021-11-03 move function implemented with a compination of linear and agular velocity
2021-11-04 fixed some erros still not work
    [move_function2.py]
2021-11-11 solved a few problems of the omnimotion function
    [move_function2.py]
2021-11-11 fixed a few problems
    [move_function2.py]
2021-11-11 proper image calibration
2021-11-11 fixed omni motional mooving
    [robot_movement.py]
2021-11-11 fixed omni motional movement
    [robot_movement.py]
2021-11-15 fixed gui issue temporary
    [robot_gui.py]
2021-11-15 impelemnted imutils, better threshold
2021-11-15 crop the frame
2021-11-18 fixed major issuer, ready for next tasks
    [image_calibration.py]
2021-11-22 fixed all github issues
    [image_calibration.py, main.py]
2021-11-25 upload electronics
    [CM1223_ESD.PcbLib, CM1223_ESD.SchLib, Con_encoder_4.SchLib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]
2021-11-25 changed dir know
    [CM1223_ESD.PcbLib, CM1223_ESD.SchLib, Con_encoder_4.SchLib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]
2021-11-25 fixed bugs from refactoring
    [image_calibration.py, main.py, robot_gui.py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]
2021-12-02 calibratong robot
2021-12-03 depth area. border of the frame is calculated now
2021-12-20 Added new version of the PCB
    [BUK6Y10-30P.SchLib, CM1223_ESD.PcbLib, CM1223_ESD.SchLib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]
2021-12-22 major issues fixed. manual controling implemented
    [main.py, manual_control.py, state_machine.py]
2021-12-22 new pcb version
    [BUK6Y10-30P.SchLib, CM1223_ESD.PcbLib, CM1223_ESD.SchLib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]
2021-12-22 added missing parts
    [NCP164CSN330T1G_Voltage_regulator.PcbLib, NCV8730_voltage_16to5V.SchLib, SAMTEC_FTSH-105-XX-X-DV.PcbLib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]
2021-12-22 github issue fix, garbage file delete
    [main.py]
2021-12-23 testing sockets
2021-12-23 Another attempt to upload the files
    [3D PCB.step, BUK6Y10-30P.SchLib, CM1223_ESD.PcbLib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]
2021-12-23 added missing files
    [MAX12930BASA&plus_.PcbLib, MAX12930BASA&plus_.SchLib, MAX14930AASE&plus_.PcbLib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]
2021-12-28 Double component
    [MAX12930BASA&plus_.SchLib]
2021-12-28 Upload the new version of the PCB
    [Mainboard.SchDoc, Motorcontroller.SchDoc, PCB1.PcbDoc]
2021-12-31 update PCB
    [BUK6Y10-30P.SchLib, CM1223_ESD.PcbLib, CM1223_ESD.SchLib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]
2021-12-31 Changes width of the silkscreen
    [PCB1.PcbDoc]
2022-01-02 add Gerber files
2022-01-19 Everything is working besides the direction of the motors
2022-01-19 interrupt handler is never called
2022-01-20 implemented PID controller
2022-01-22 git conflict fix
    [3D PCB.step, BUK6Y10-30P.SchLib, CM1223_ESD.PcbLib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]
2022-01-22 calibration of the thrower
2022-01-23 upload main software for the stm32
2022-02-06 huge rafctoring before final
    [CM1223_ESD.PcbLib, CM1223_ESD.SchLib, Con_encoder_4.SchLib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]

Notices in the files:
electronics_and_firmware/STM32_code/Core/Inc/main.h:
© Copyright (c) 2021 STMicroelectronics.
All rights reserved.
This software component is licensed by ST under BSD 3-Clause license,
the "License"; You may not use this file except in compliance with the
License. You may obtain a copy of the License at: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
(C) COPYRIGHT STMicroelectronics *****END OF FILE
